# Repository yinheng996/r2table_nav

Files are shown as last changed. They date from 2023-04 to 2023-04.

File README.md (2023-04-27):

# Robotic Food Delivery System

This is an open-source project for a Robotic Food Delivery System, developed as part of the __EG2310 Fundamentals of System Design__ module, Sem 2 AY22/23, under the _Innovation and Design Programme (iDP)_ at National University of Singapore (NUS).

The project team, Studio 2 Group 3, comprises of Loh Yin Heng, Wang Bo, Jeanette Sim Yu, Hang Jin Guang, and Ananya Agarwal.

## Description
Our objective is to build a food delivery robot that seamlessly navigates through a restaurant, collects an order, and delivers it to the designated table. Our design is based on the Turtlebot 3 platform and utilizes ROS 2 Foxy as its operating system. We employ the MQTT messaging protocol for inter-system communication.

To achieve our objective, we have built a dispenser equipped with a keypad that allows for the selection of the table. Our dispenser is powered by an ESP32 microcontroller, which serves as the brain of the dispenser. This allows for seamless communication between the dispenser and the robot, and enables us to easily modify and update the dispenser's functionality.
<br>
<br/> <p align="center">
     
<br/>

<br>This repository houses the code for robot navigation, MQTT communication and dispenser functions.
You may check out our project report under the [/Documentations](https://github.com/yinheng996/r2table_nav/tree/main/Documentations) folder for more details on our robot and its mission.

## Important Files
* [disp_code.ino](https://github.com/yinheng996/r2table_nav/blob/main/ESP32_disp/disp_code.ino) - This file serves as the dispenser master script, responsible for powering the entire dispenser. It encompasses a range of functions including integration of the keypad, servo, and limit switch, in addition to the publisher code for MQTT. <br/>
* [limit_switch.py](https://github.com/yinheng996/r2table_nav/blob/main/py_pubsub_robot/limit_switch.py) - This file contains the code to be run on the RPi. It is in charge of publishing the limit switch status out to the remote laptop to let the remote laptop know when food has been removed from the carrier and to return to the dispenser so that it can take the next order.<br/>
* [r2tcheckpt_nav.py](https://github.com/yinheng996/r2table_nav/blob/main/table_nav/table_nav/r2tcheckpt_nav.py) - This file the master navigation script that we run on the laptop. It subscribes to MQTT and ROS topics and navigates the TurtleBot based on Table Number inputted on the dispenser. The main functions used to navigate around the restaurant setting is `move_til()` and `right_angle_rotate()`.  The important functions used to complete the task includes `connect_mqtt()`, `docking()`, `check_dist()`, `calibrate()` and `locate_table6()` <br/>
* [ESP32_test](https://github.com/yinheng996/r2table_nav/tree/main/ESP32_test) - This folder contains a series of C++ files that facilitate testing of the hardware functionality on the dispenser. Included are files to test the ESP32 blink, keypad, limit switch, MQTT publisher, servo and wifi setup.
* [r2factory_test.py](https://github.com/yinheng996/r2table_nav/blob/main/table_nav/table_nav/r2factory_test.py) -  This file contains a set of tests designed to verify the functionality of the TurtleBot. Upon execution, step-by-step instructions are displayed on the terminal for users to follow along.

## Preparation
### Installation
1. Follow the instructions here to setup ROS 2 Foxy on laptop and TurtleBot. <br/>
    (You may stop once you are able to teleoperate the TurtleBot from your computer.) <br/> 
    https://emanual.robotis.com/docs/en/platform/turtlebot3/quick-start/
2. Follow the instructions here to download, install and setup MQTT X on your laptop. <br/>
    (We are using a cloud-based MQTT desktop client for this project (MQTT X) for better consistency.) <br/> 
    https://github.com/emqx/MQTTX/blob/main/docs/manual.md <br/>
   Refer to our project configurations [here](https://github.com/yinheng996/r2table_nav/blob/main/Documentations/MQTT%20X%20Setup%20Config.pdf)
3. Follow the instructions here to setup ESP32 software. <br/> 
    https://esp32io.com/tutorials/esp32-software-installization
5. Follow the instructions here to setup Arduino IDE on your laptop. <br/> 
    https://www.arduino.cc/en/software <br/>
    Install the follow libraries on your Arduino IDE:
    * PubSubClient by Nick O'Leary
    * EspMQTTClient by Patrick
    * Keypad by Mark
    * ESP32Servo by Kevin
    * ezButton by ArduinoGetStarted.com
5. Follow the instructions here to setup Paho-MQTT on your laptop. <br/>
https://pypi.org/project/paho-mqtt/
6. Refer to our [/Hardware/Electrical Circuits](https://github.com/yinheng996/r2table_nav/tree/main/Hardware/Electrical%20Circuits) folder for the schematics of the circuits that we use to replicate our robot and dispenser system. <br/>
7. Refer to our [/Hardware/Mechanical Parts](https://github.com/yinheng996/r2table_nav/tree/main/Hardware/Mechanical%20Parts) folder for the fabrications and assembly that we use to replicate our robot and dispenser system. <br/>

__Important__: Please note that our project has been developed using Ubuntu 20.04.4, ROS2 Foxy, Arduino 2.1.0 and Python 3.6, as well as a DOIT ESP32 Devkit V1 Board and a Robotis Co. TurtleBot3 Burger with Raspberry Pi 3B+. As such, modifications may be necessary when using other software systems or hardware platforms.

### Setup

1. To setup your Ubuntu Machine, clone our repository into your Home directory. Compile the workspace. <br/>

    ```
    cd colcon_ws/src/auto_nav
    git clone https://github.com/yinheng996/r2table_nav.git 
    cd colcon_ws
    colcon build
2. To setup your TurtleBot, copy the `/py_pubsub` folder onto the Raspberry Pi. Compile the workspace. <br/>
    
    ```
    ssh ubuntu@<RPi IP address>
    scp -r <path to r2table_nav directory>/py_pubsub ubuntu@<RPi IP address>:~/turtlebot_ws/src 
    cd turtlebot3_ws
    colcon build 
3. To setup the ESP32, we will use the Arduino IDE.
    1. Open the code for the ESP32 in the Arduino IDE. This will be located in the repository that you cloned in step 1. In the code, make any necessary changes or modifications.
    2. Connect the ESP32 to your computer using a USB cable.
    3. In the Arduino IDE, select the correct board and serial port. To do this, navigate to `Tools` -> `Board` and select `ESP32 Dev Module`. Then, navigate to `Tools` -> `Port` and select the correct serial port.
    4. To upload the code onto the ESP32, click on the `Upload` button in the Arduino IDE and hold down BOOT button on esp32, release the button once u see "connecting" in the serial monitor.
    5. Once the upload is complete, disconnect the ESP32 from your computer and power it using an external power source. The code should now be running on the ESP32.
4. To setup MQTT X, launch the MQTT X Desktop Client
    1. After the connection to ESP32 is successful, click the `New Subscription` button in the lower left corner to add New Topics. <br/>
    2. Add the topics `docking` and `table_num`
## System check

#### For your TurtleBot
We need to test if the limit switch is connected to the RPi and if the RPi is able to publish its status using [limit_switch.py](https://github.com/yinheng996/r2table_nav/blob/main/py_pubsub_robot/limit_switch.py)
##### In one terminal
    ssh ubuntu@<RPi IP address>
    roslaunch turtlebot3_bringup turtlebot3_robot.launch
##### In another terminal
    ssh ubuntu@<RPi IP address>
    cd <path to r2table_nav directory>/py_pubsub
    python3 limit_switch.py
The terminal should start publishing the limit switch state, press and release the limit switch and check if the publisher updates the limit switch state.
If not, reboot your TurtleBot and repeat the TurtleBot system Check.
#### For your Laptop
We need to run a factory test on the TurtleBot from the Laptop to test if the laptop is able to communicate with the RPi and if all components of the TurtleBot is functional using [r2factory_test.py](https://github.com/yinheng996/r2table_nav/blob/main/table_nav/table_nav/r2factory_test.py).
##### In one terminal
    cd <path to r2table_nav directory>/table_nav/table_nav
    python3 r2factory_test.py
Follow the instructions printed on your terminal, and if everything works out fine, it means the system is ready to go.
#### For your ESP32
We need to run a factory test on the ESP32. <br/>
   Launch the ESP32 factory test scripts in our [/ESP32_test](https://github.com/yinheng996/r2table_nav/tree/main/ESP32_test) folder onto your Arduino IDE, then upload and run on your ESP32 module. <br/>
   Do this individually for each script. <br/>
   If your ESP32 module passes all the tests, it is ready to go.
#### For your MQTT X
We need to check if the MQTT is able to received messages from the ESP32. <br/>
   Launch the MQTT desktop client. <br/>
   Check for messages received from the ESP32 Publisher. If nothing is received, refresh the desktop client. <br/>

## Operation Parameters
From lines 15 to 41 of [/table_nav/table_nav/r2tcheckpt_nav.py](https://github.com/yinheng996/r2table_nav/blob/main/table_nav/table_nav/r2tcheckpt_nav.py)

The explanation of all the parameters are as commented below. These are the values which we found work the best for us in our use case. Please change these values if you require a different behavior of the robot.

    # Constants
    FAST_ROTATION_SPEED = 0.5 # speed of fast rotation, mainly for regular turns
    SLOW_ROTATION_SPEED = 0.2 # speed of slow rotation, mainly for calibrations
    MOVING_SPEED = 0.18 # speed of linear movements

    LIDAR_FRONT_OFFSET = 0.193 # distance from lidar to front of robot
    LIDAR_BACK_OFFSET = 0.094 # distance from lidar to back of robot
    DISPENSER_WALL_DISTANCE = 0.50 # distance from centre of dispenser to wall
    STOP_DISTANCE = 0.1 + LIDAR_FRONT_OFFSET # distance to stop from Table

    CORF_OFFSET = 0.152 # distance from centre of rotation to front of robot
    CORB_OFFSET = 0.13 # distance from centre of rotation to back of robot

    DOCKING_DIST = 0.178 # distance to stop from docking station

    MOVE_DIST_F = LIDAR_FRONT_OFFSET + 0.21 # movement offset at speed 0.18 from front
    MOVE_DIST_CORF = MOVE_DIST_F - CORF_OFFSET # movement offset at speed 0.18 from centre of rotation from front
    MOVE_DIST_B = LIDAR_BACK_OFFSET + 0.24 # movement offset at speed -0.18 from back
    MOVE_DIST_CORB = MOVE_DIST_B - CORB_OFFSET # movement offset at speed -0.18 from centre of rotation from back

    SWEEP_ANGLE = 30 # angle to sweep for Table
    ANGLE_RANGE = range(-SWEEP_ANGLE, SWEEP_ANGLE + 1) # range of angles to sweep for Table

    LIDAR_DATA_FILE = 'lidar.txt' # file to store lidar data logged
    MAP_DATA_FILE = 'map.txt' # file to store map data logged

    CAN_DROP = 4 # seconds to wait before can is dropped

From lines 43 to 49 of [/table_nav/table_nav/r2tcheckpt_nav.py](https://github.com/yinheng996/r2table_nav/blob/main/table_nav/table_nav/r2tcheckpt_nav.py)

Please input your MQTT configurations, especially your username and password.

    # MQTT variables
    MQTT_BROKER = "broker.emqx.io"
    MQTT_PORT = 1883
    MQTT_USERNAME = "idpgrp3" # username for MQTT broker
    MQTT_PASSWORD = "turtlebot" # password for MQTT broker
    MQTT_TOPIC_TABLENUM = "table_num" # topic to subscribe to for table number
    MQTT_TOPIC_DOCKING = "docking" # topic to subscribe to for docking

## Running the Code
A total of __4 terminals__ would be required to run the code, in addition to the __MQTT X desktop client__. <br/> 
Prior to commencing the operation, ensure that a stable WiFi connection is established and that all devices, including the ESP32, laptop, and TurtleBot, are connected to the same WiFi network. It is critical to verify that all electrical connections are secure, and all mechanical mountings on both the TurtleBot and Dispenser are firmly in place before initiating the operation. <br/>
__To ensure reliable and safe performance, it is advised to avoid any physical contact with the system during operation.__ <br>
##### In Terminal 1: To bring up TurtleBot3
    ssh ubuntu@<RPi IP address>
    roslaunch turtlebot3_bringup turtlebot3_robot.launch
##### In Terminal 2: To host Bot Limit Switch Publisher
    ssh ubuntu@<RPi IP address>
    cd <path to r2table_nav directory>/py_pubsub_robot
    python3 limit_switch.py
##### In Terminal 3: To host IR Sensor Publisher
    ssh ubuntu@<RPi IP address>
    cd <path to r2table_nav directory>/py_pubsub_robot
    python3 IR.py
##### In Terminal 4: To run navigation code
    cd <path to r2table_nav directory>/table_nav/table_nav
    python3 r2tcheckpt_nav.py
#### In MQTT X:
* Launch MQTT X and select `connect`. <br/>
<br>
The system is ready to go. Press a number from 1-6 on the keypad for Food Delivery.

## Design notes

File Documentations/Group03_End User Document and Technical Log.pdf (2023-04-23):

EG2310 GROUP 3 END USER DOCUMENT AND TECHNICAL LOG

### 1. General System Description and Critical Data

Purpose: The Dispenser and Delivery Robot System allows a can to be loaded, dispensed, and then delivered to a table chosen by the user.

### 1.1 Dispenser

The Dispenser allows the user to load a can, choose the table number for delivery. It then transfers the can to the Delivery Robot.
Model | Custom-made in-house
Overall Weight | 1.64 kg
Overall Centre of Gravity w/o can (x,y,z) | (35.59, 82.25, 30.16)
Overall Dimension LxWxH (mm) | 93x178x207
Power Specification | 4x AAA Batteries

### 1.2 Delivery Robot

The Delivery Robot is designed to receive a ⌀66mm drink can of length 115mm, approx weight 350g from the Dispenser and delivers it to the table chosen by the user. The manufacturer does not guarantee the usability of this robot for cans of different dimensions and/or weights.
Model | ROBOTIS TurtleBot 3 Burger adapted with custom-made Drink Can Carrier Assembly
Software Version | Ros2 Foxy
Overall Weight | 1.3kg
Overall Centre of Gravity w/o can (x,y,z) | (5.5,0,5.5)
Overall Dimension LxWxH (mm) | 235x178x192
Power Specification | LiPo Battery 11.1V 1,800mAh

Refer to TurtleBot3 Burger Specifications found on ROBOTIS e-Manual website: https://emanual.robotis.com/docs/en/platform/turtlebot3/features/#specifications

### 1.3 Instructions for User

1) Place Dispenser at the designated spot on the arena such that its center is 50cm from the side wall and the Electronics Platform is flush to the back wall of the designated spot.
2) Place the Delivery Robot in front of the Dispenser such that the front of the LiDAR is facing the Dispenser and the V-shaping Homing Plate on Delivery Robot is inside the Dispenser’s V-shaping Homing Plate. Do not press any buttons before this is done.
3) Load the can in the Dispenser. Do not drop in the can, place it lightly in the carrier, flushed close to the servo-side.
4) Press the button labeled ‘EN’ on the ESP32 board.
5) Press the button on the keypad to indicate the table number. Do not press the button multiple times. You can only press table number 1-6 and each table can only be chosen once. If a table that has been chosen before must be chosen again, follow steps in 1.4
6) Dispenser will load the can into the robot, and the robot will travel to the designated table. It may go near other tables, please wait until it reaches the desired table and the wheels have stopped rotating to pick up the can.
7) Collect the can after the robot comes to a full stop within 15cm of the designated table.
8) Wait for the Delivery robot to return to the dispenser and dock with the dispenser.
9) Repeat Steps 5-9 for subsequent tables.

### 1.4 Repeating a table

1) On the back-end laptop, press ctrl+C. Press the arrow up key and press enter.

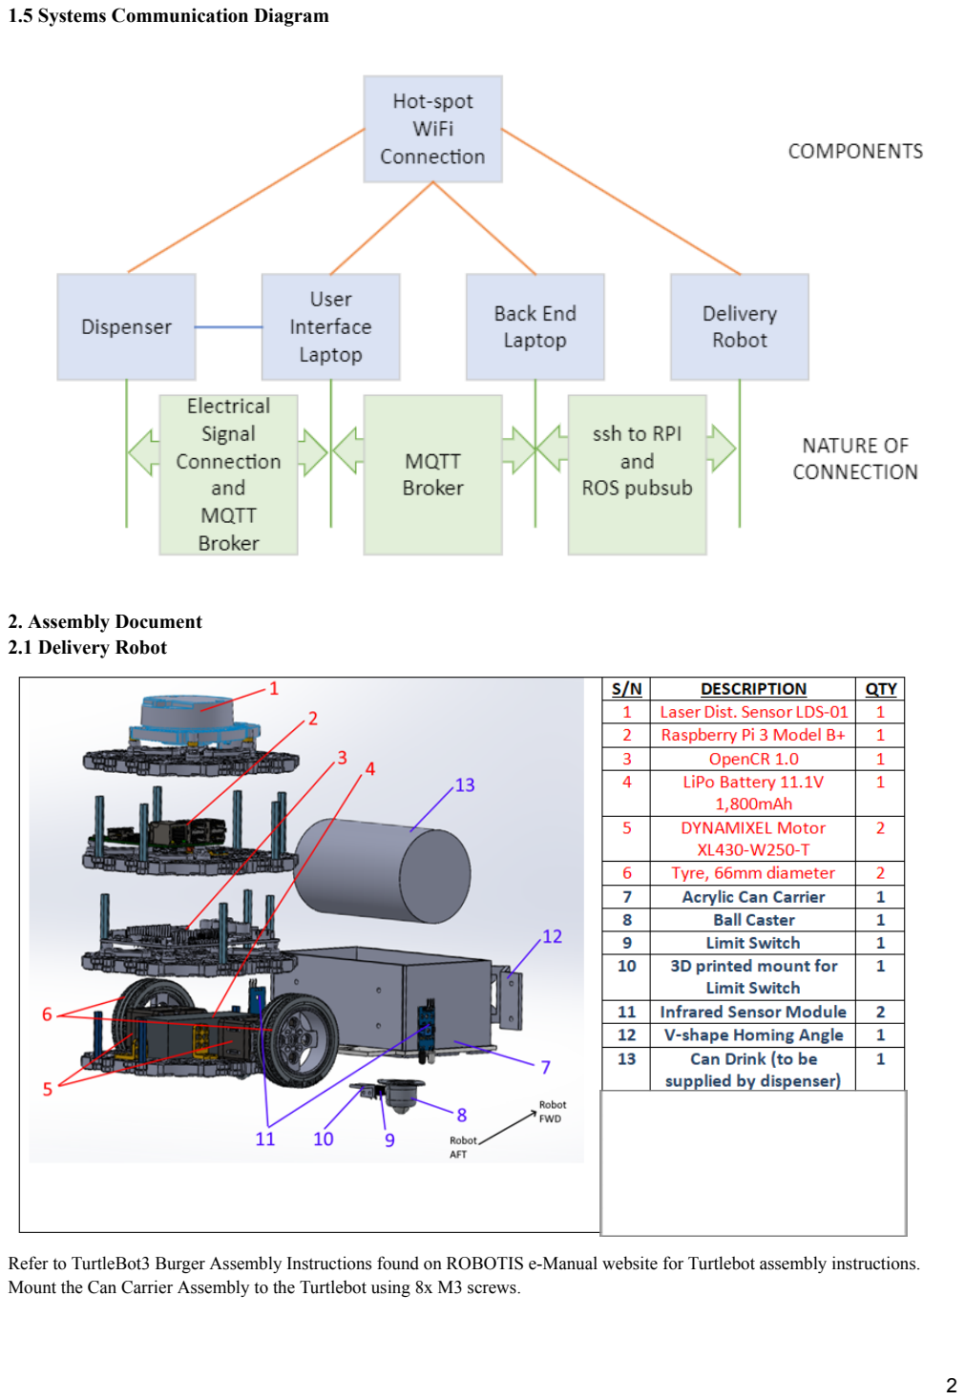
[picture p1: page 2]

### 1.5 Systems Communication Diagram

### 2. Assembly Document 2.1 Delivery Robot

Refer to TurtleBot3 Burger Assembly Instructions found on ROBOTIS e-Manual website for Turtlebot assembly instructions. Mount the Can Carrier Assembly to the Turtlebot using 8x M3 screws.

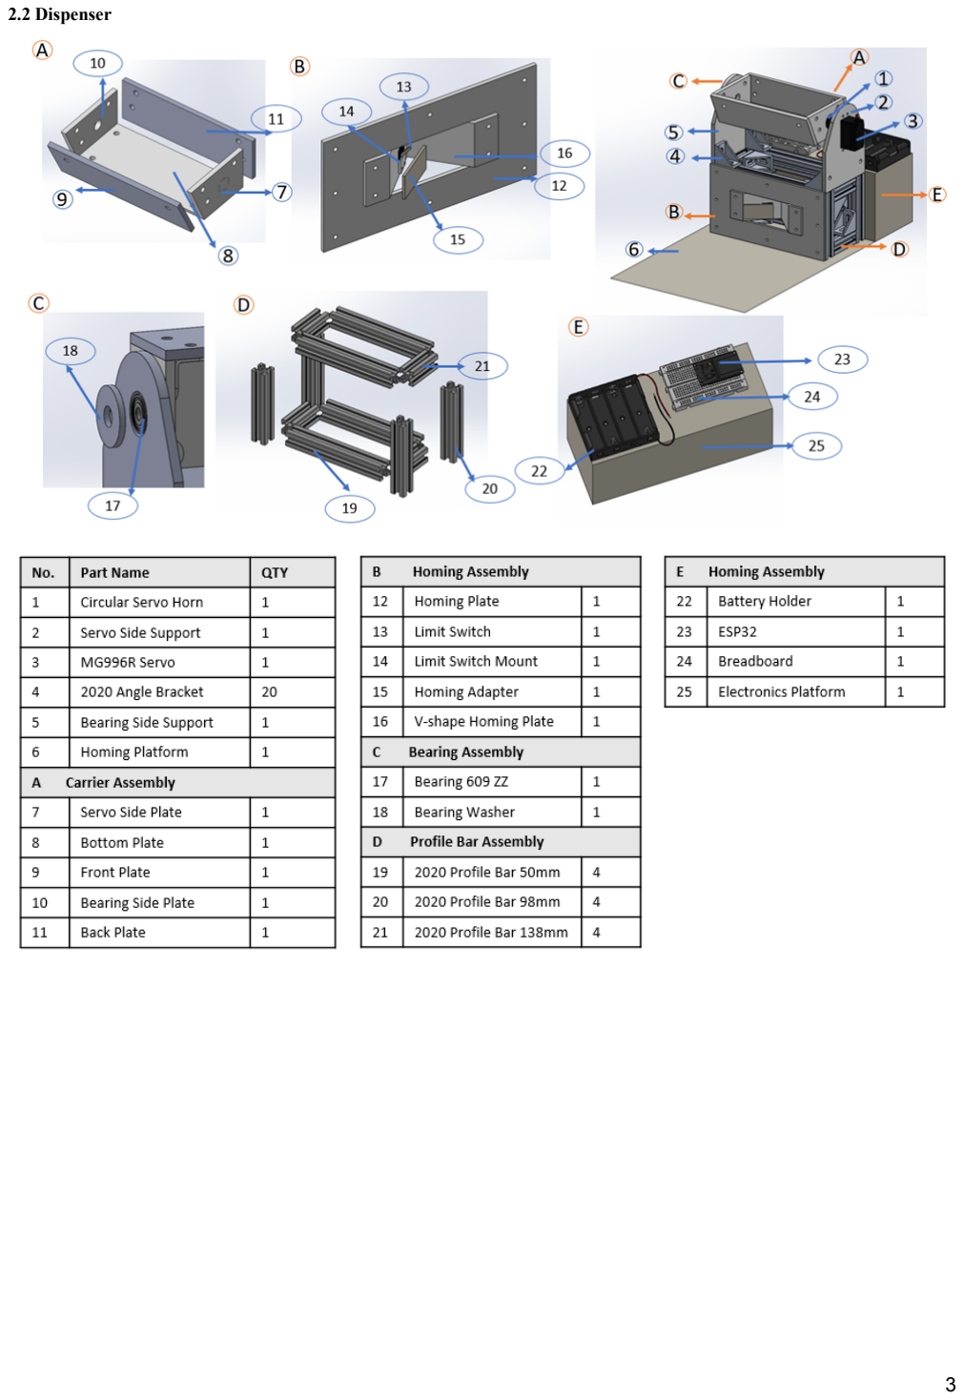
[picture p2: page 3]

### 2.2 Dispenser

### 3. Acceptable Defect Log

### 3.1 Dispenser

Defect Description | Acceptable Criteria | Defect Classification
Critical | Major | Minor
Dispenser carrier has gaps between its faces | This does not pose any effects on its structural integrity, strength of holding the can, and general function | | X
Homing Angle has a cardboard piece taped inside | This serves to facilitate the homing | | | X
Profile bar base has slight misalignment | This does not affect its structural integrity | | | X
The nut for the bearing is a little lose | This is to ensure tolerancing for proper function of the roller bearing | | X

### 3.2 Delivery Robot

Defect Description | Acceptable Criteria | Defect Classification
Critical | Major | Minor
There is acrylic glue holding the plates of the Delivery Robot’s carrier together but there are slight gaps | Tape is used to ensure the carrier is secure | | | X
LiDAR scanning is not accurate | We have calibration code to check that the LiDAR is operating correctly in relation to its surroundings. | | X

### 4. Factor Acceptance Test

### 4.1 Dispenser

Test Procedure and Objectives | Acceptable Criteria | Acceptable (Y/N)

Physical Checks

Shake test | When the Dispenser is shook, no cables come loose, no parts fall out, no screws fall out
Safety Check | No signs of damage on the cables Cables are routed neatly and are not in the way of the Dispenser Carrier’s motion
Common Ground | Ensure all components are connected to common ground

Electronics Components Checks

Connect a laptop with the Arduino IDE, running ‘ESP32_final_mqtt_pub_test’ to the ESP32

Verify Batteries are in working condition | Use multimeter to ensure batteries that the sum of the 4 AA Batteries sum to at least 4.8 V
Verify that the limit switch works | Press down the limit switch. Serial Monitor on laptop screen should print ‘Limit switch activated! Robot is here, waiting for

| keypad input…’
Verify that the keypad works | Press any key from 1 to 6. Serial Monitor on laptop screen should print ‘Table number for delivery: [keypad input]’
Verify that the Servo motor works | After the laptop screen prints ‘Robot is receiving table number...’, it should print ‘Tilting…’ and the servo should turn the Dispenser Carrier

### 4.2 Delivery Robot

Test Procedure and Objectives | Acceptable Criteria | Acceptable (Y/N)

Physical Hardware Checks

Shake test | When the Delivery Robot is shook, no cables come loose, no parts fall out, no screws fall out
Safety Check | No signs of damage on the cables
Turn on Delivery Robot | 1. Green light on the OpenCR 2. Sequence of beeps in when Turtlebot is turned on 3. RPI Green Light is on

Electronics Components Checks

Verify that the RPi works | Sshrp to the RPI Terminal should return ‘Welcome to Ubutntu [...]’ RPI flashes a red light to show power is connected RPI flashes a green light to show SD card is being read
Verify that the OpenCR works | Sequence of beeps when the delivery robot is turned on
Verify that the Dynamixel motors work | Key in ros2 run turtlebot3_teleop teleop_keyboard The following commands can be used to observe that the movement is as expected W for forward S for Stop D for turning right A for turning left X for backwards
Verify that the IR Sensor Module is operational | The IR sensor on one side should be light up green and the other side should light up red.
Verify that the LiDAR is calibrated correctly | Key in python3 r2lidar_calib.py Key in ‘0’ and place an object at the physical ‘0’ degree of the LiDAR. The LiDAR should be logging a sudden decrease in distance (0.21), which indicates that the angle is calibrated. Repeat for 180 degrees, you should see the distance as 180 degrees

### 5. Maintenance and Part Replacement Log

FOUND BY/DATE /TIME/SIGN | REASON PLACED UNSERVICEABLE | DETAILS OF ACTION TAKEN | DATE/ TIME | TRADESMAN NAME/SIGN
HANG JG 30/3/23 2030H | BATTERY UNABLE TO CHARGE. | BATTERY REPLACED. | 30/3/23 2045H | HANG JG

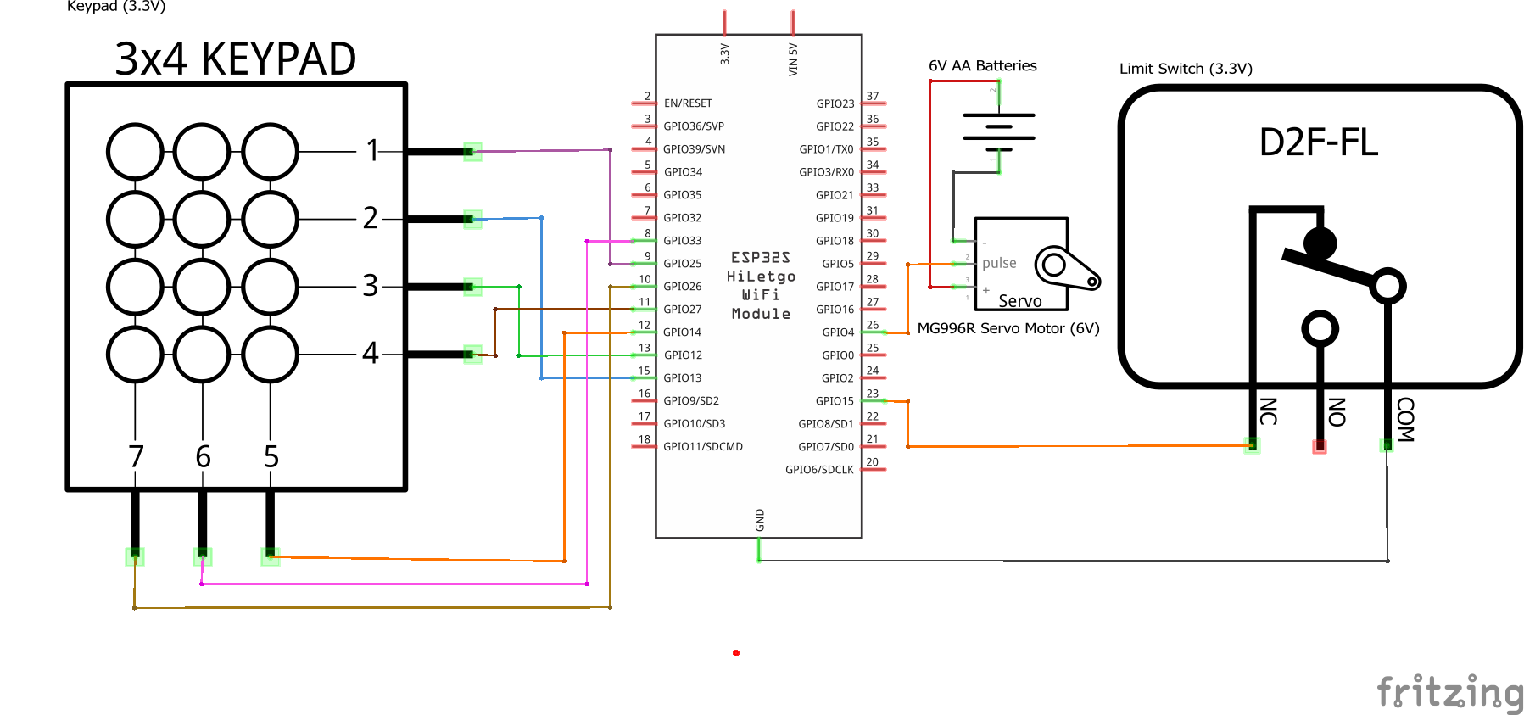
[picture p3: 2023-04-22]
Hardware/Electrical Circuits/ESP32_WROOM_32 Dispenser System - Schematics.png

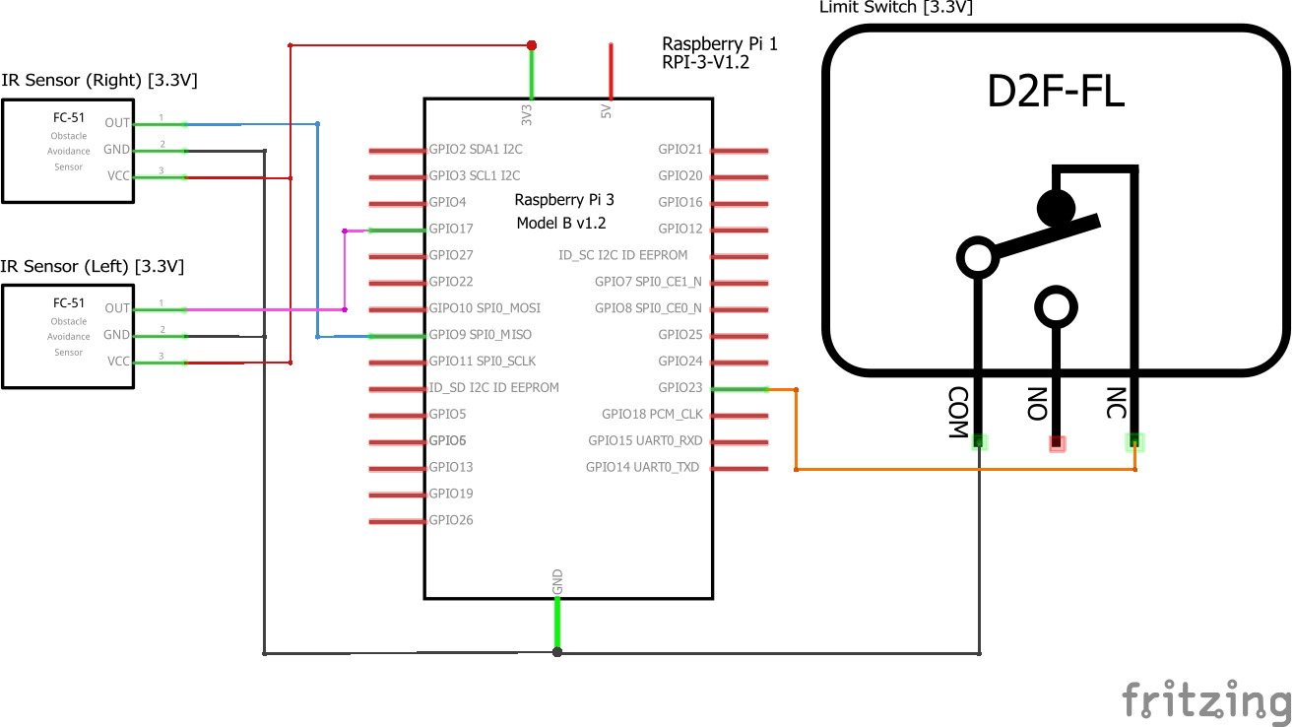
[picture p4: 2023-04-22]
Hardware/Electrical Circuits/Delivery Robot System - Schematics.png

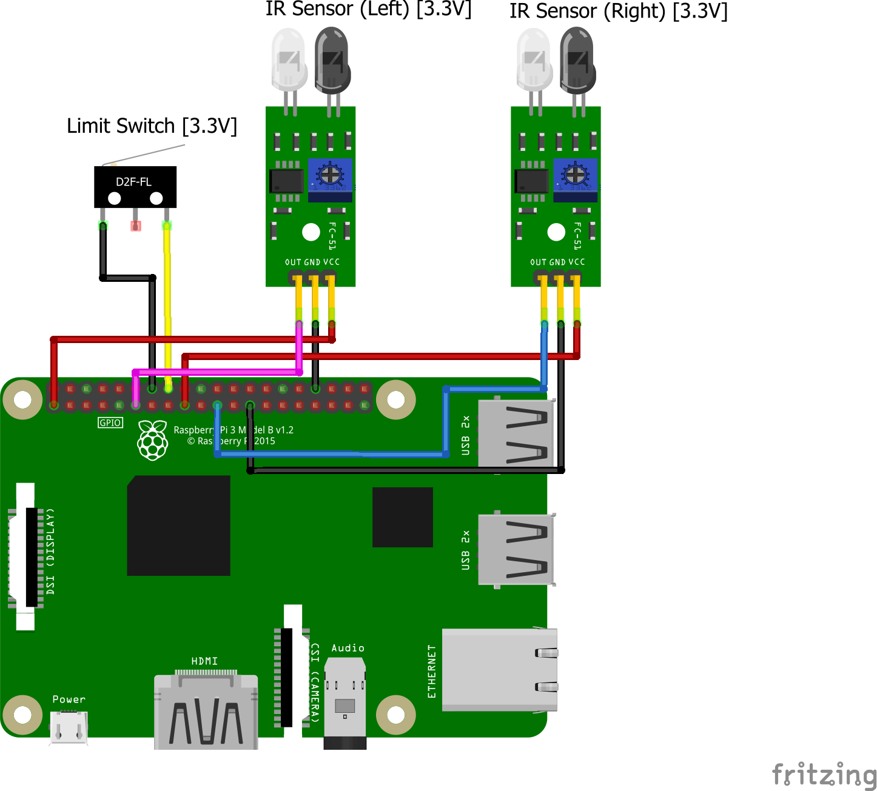
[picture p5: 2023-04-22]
Hardware/Electrical Circuits/Delivery Robot System - Breadboard.png

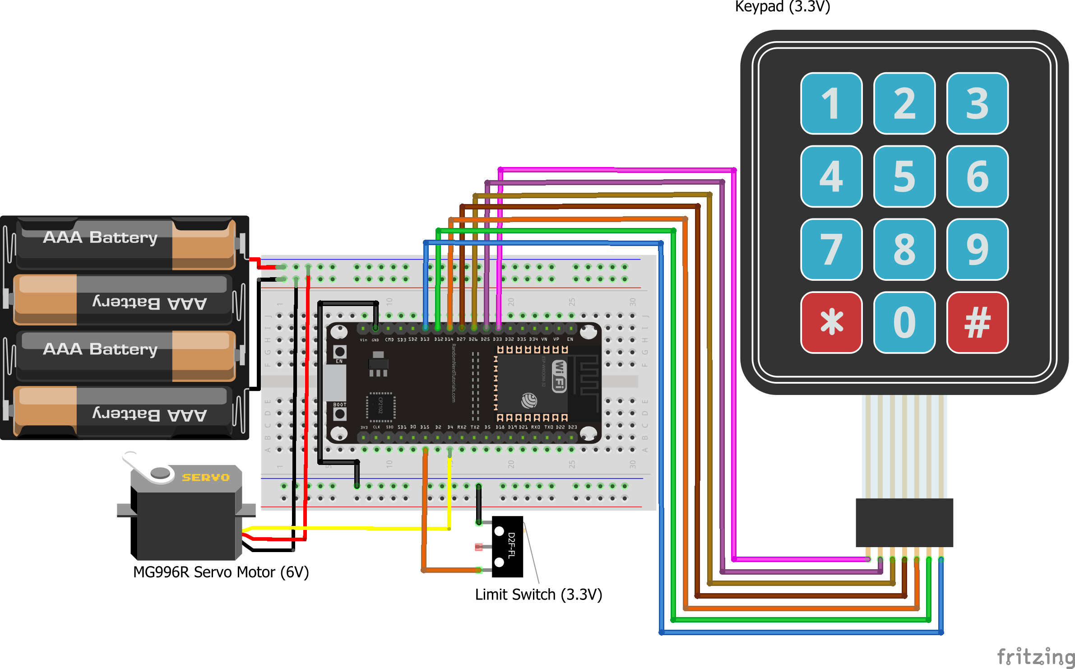
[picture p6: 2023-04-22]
Hardware/Electrical Circuits/ESP32_WROOM_32 Dispenser System - Breadboard.png

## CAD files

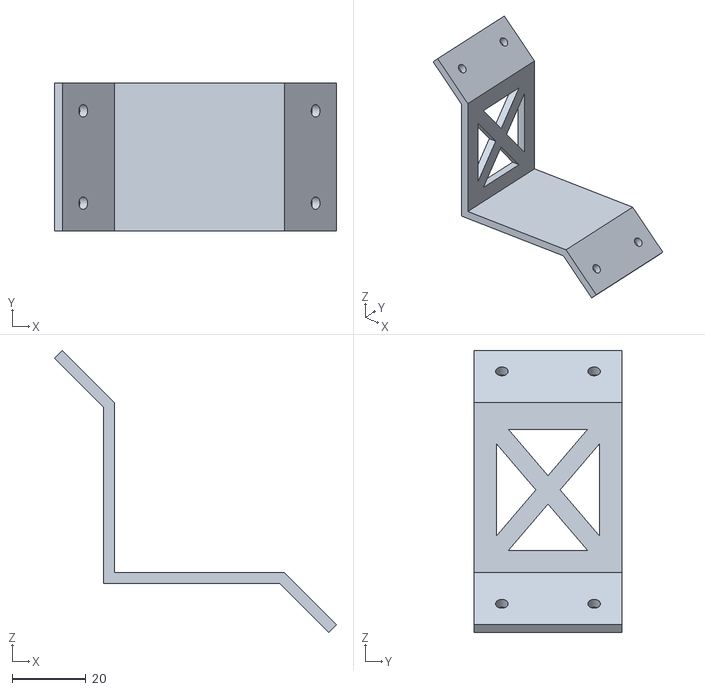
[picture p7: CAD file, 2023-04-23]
Hardware/Mechanical Parts/3D_Print/Homing L Robot-side Split.STL
76.4 x 40.0 x 76.4

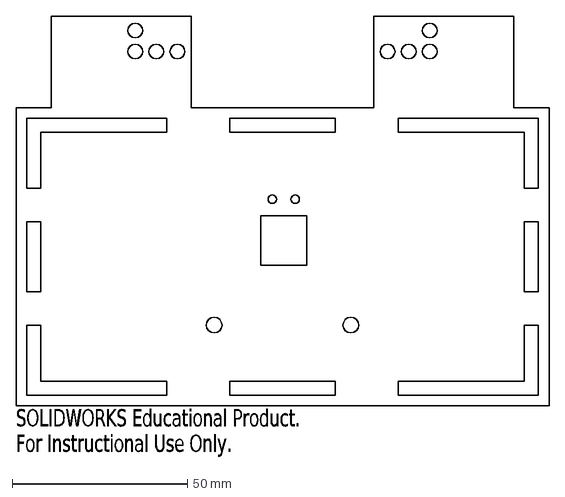
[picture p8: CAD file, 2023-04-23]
Hardware/Mechanical Parts/Robot_Can_Carrier/[Trayv2] Base_T5_Qty1.DXF
SOLIDWORKS Educational Product.
For Instructional Use Only.

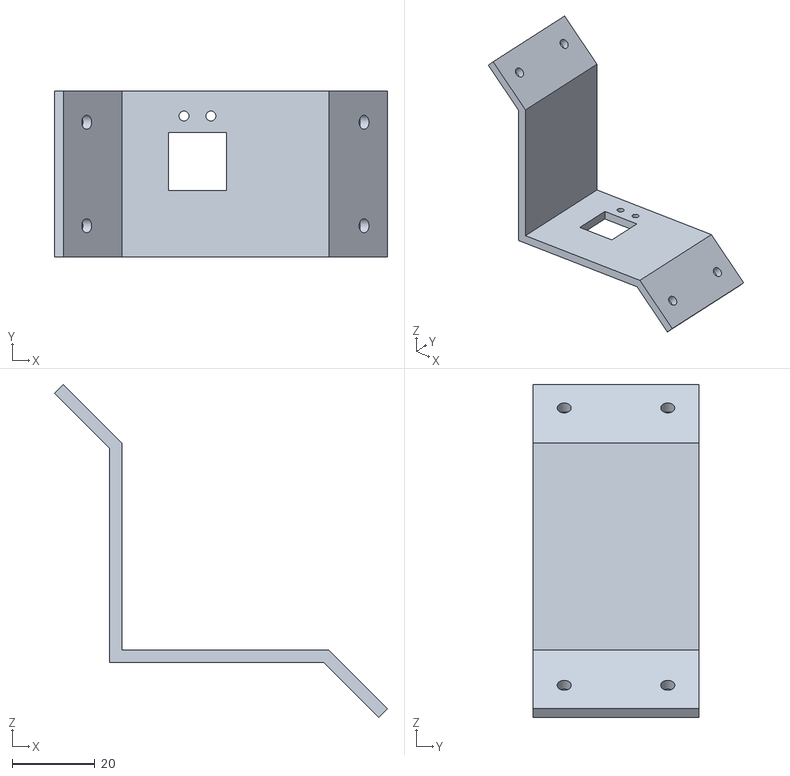
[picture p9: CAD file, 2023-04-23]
Hardware/Mechanical Parts/3D_Print/Homing L.STL
80.4 x 40.0 x 80.4

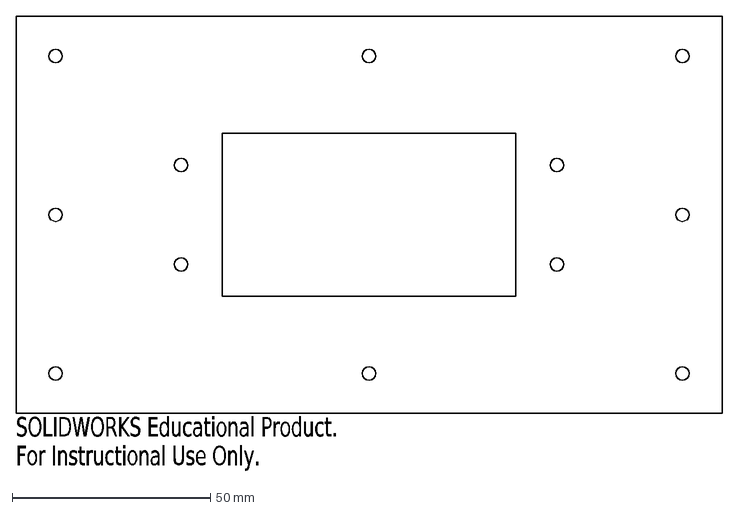
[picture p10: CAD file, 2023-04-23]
Hardware/Mechanical Parts/Dispenser/Robot Homing Plate_T3mm_QTY1.DXF
SOLIDWORKS Educational Product.
For Instructional Use Only.

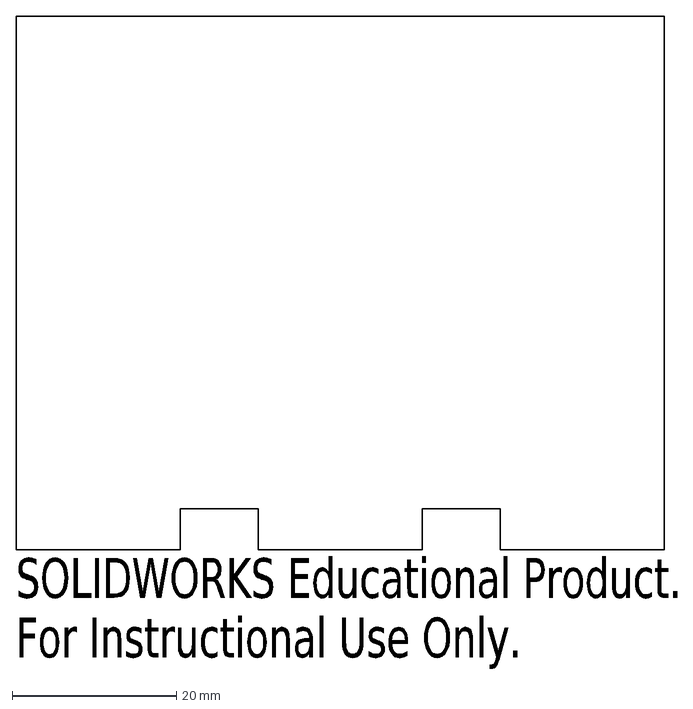
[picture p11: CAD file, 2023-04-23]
Hardware/Mechanical Parts/Robot_Can_Carrier/[Trayv2] short side_T3_Qty2.DXF
SOLIDWORKS Educational Product.
For Instructional Use Only.

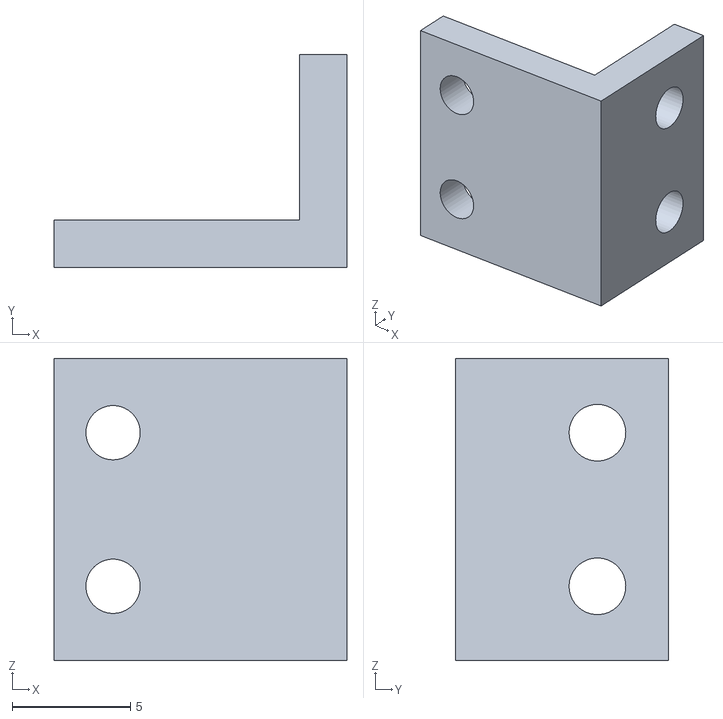
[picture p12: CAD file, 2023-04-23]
Hardware/Mechanical Parts/3D_Print/Limit Switch Mount Dispenser.STL
12.4 x 9.00 x 12.8

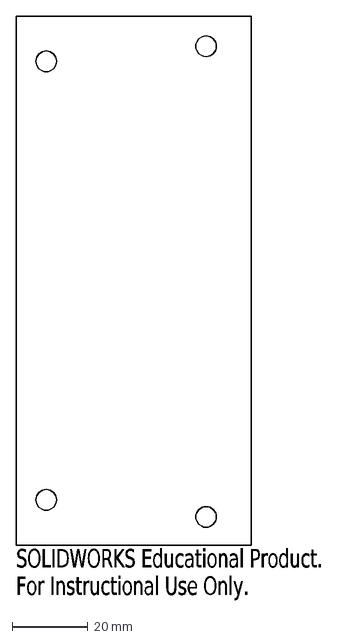
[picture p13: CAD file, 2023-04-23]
Hardware/Mechanical Parts/Dispenser/Bucket Base2_T5_QTY1.DXF
SOLIDWORKS Educational Product.
For Instructional Use Only.

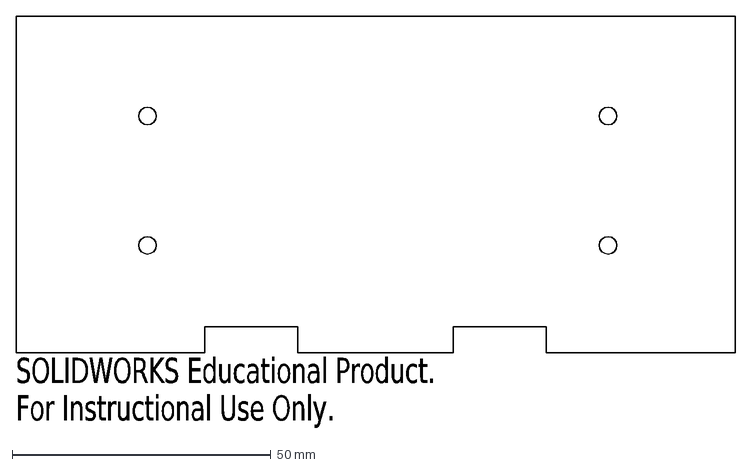
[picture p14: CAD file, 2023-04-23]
Hardware/Mechanical Parts/Robot_Can_Carrier/[Trayv2] Long side_T3_Qty2'.DXF
SOLIDWORKS Educational Product.
For Instructional Use Only.

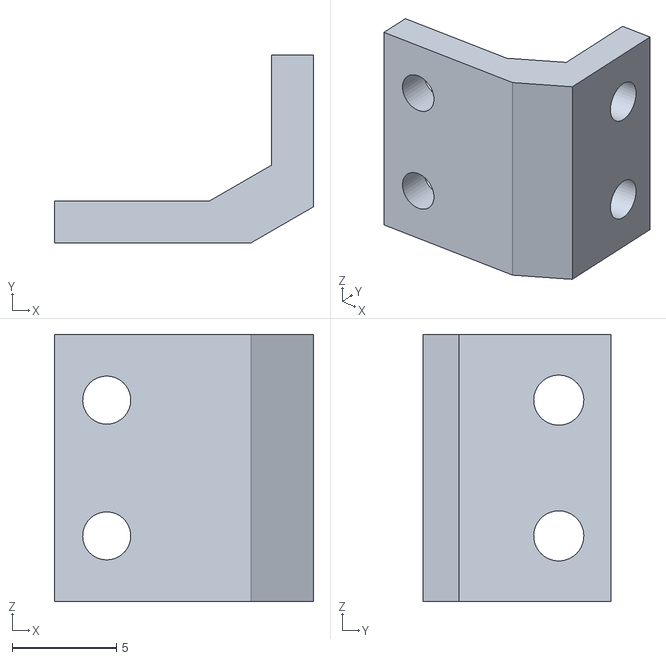
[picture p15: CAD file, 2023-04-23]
Hardware/Mechanical Parts/3D_Print/Limit Switch Mount Carrier.STL
12.4 x 9.00 x 12.8

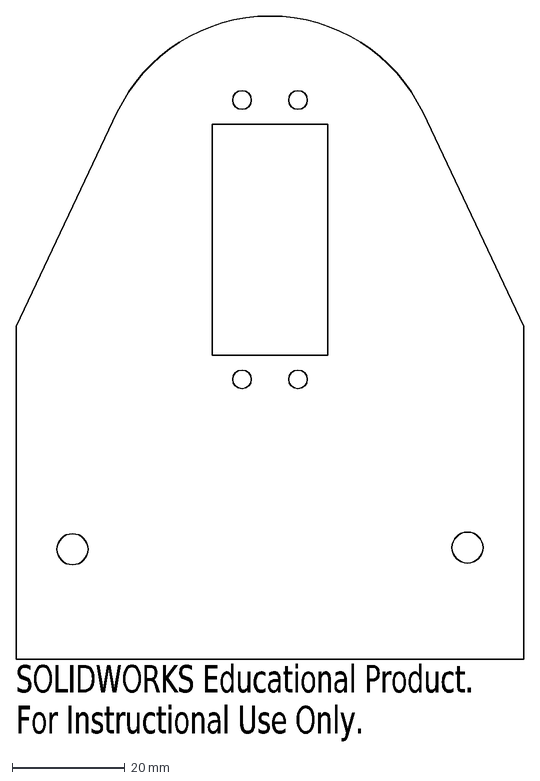
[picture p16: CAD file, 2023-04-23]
Hardware/Mechanical Parts/Dispenser/Side Support Servo Side Fri_T5_QTY1.DXF
SOLIDWORKS Educational Product.
For Instructional Use Only.

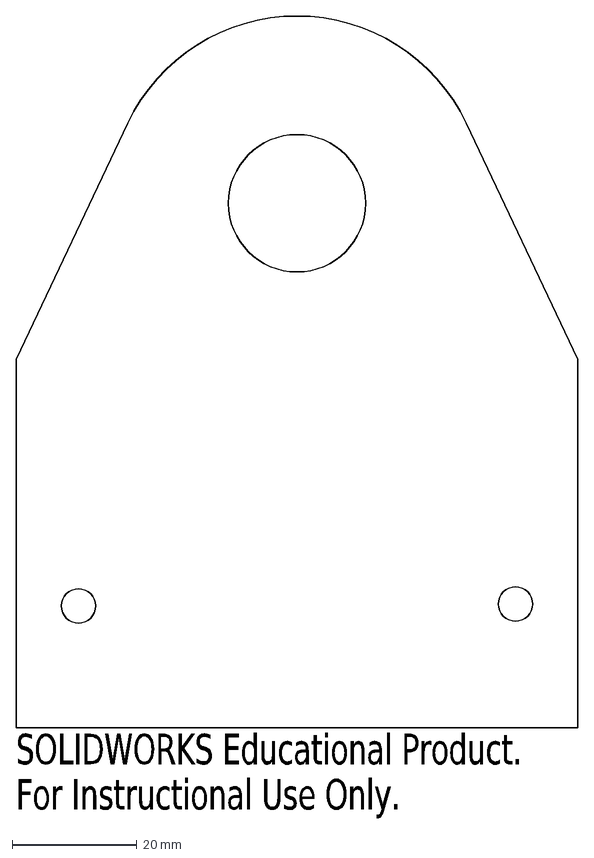
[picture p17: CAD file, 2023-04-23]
Hardware/Mechanical Parts/Dispenser/Side Support Bearing Side Fri_T5_QTY1.DXF
SOLIDWORKS Educational Product.
For Instructional Use Only.

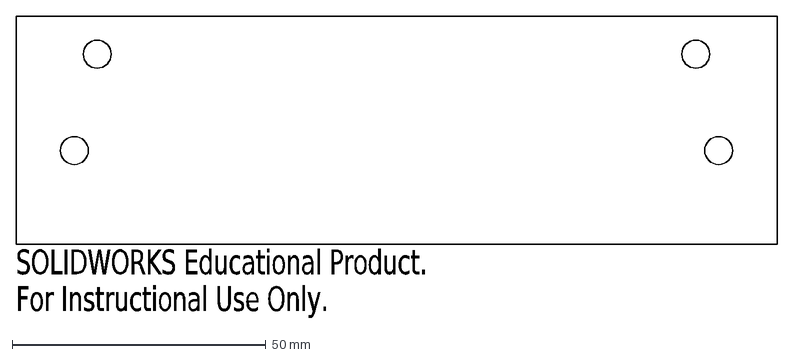
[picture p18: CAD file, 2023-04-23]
Hardware/Mechanical Parts/Dispenser/Back Carrier Acrylic_T5_QTY1.DXF
SOLIDWORKS Educational Product.
For Instructional Use Only.

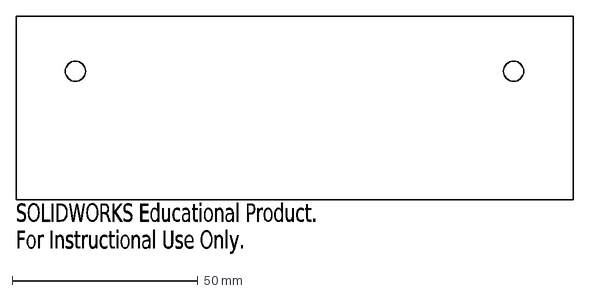
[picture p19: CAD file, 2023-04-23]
Hardware/Mechanical Parts/Dispenser/Front Carrier_T5_QTY1.DXF
SOLIDWORKS Educational Product.
For Instructional Use Only.

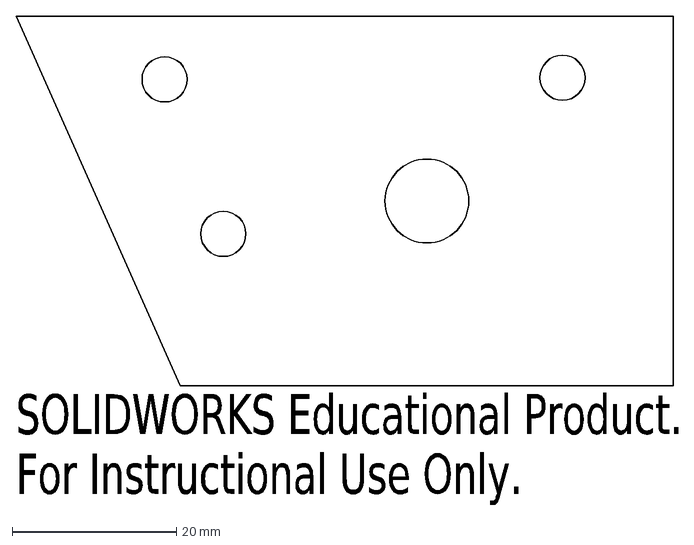
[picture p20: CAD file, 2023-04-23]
Hardware/Mechanical Parts/Dispenser/Bucket Bearing Side_T5_QTY1.DXF
SOLIDWORKS Educational Product.
For Instructional Use Only.

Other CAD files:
Hardware/Mechanical Parts/Dispenser/Bucket Servo Side_T5_QTY1.DXF
Hardware/Mechanical Parts/Dispenser/Bearing Washer_T3_QTY2.DXF

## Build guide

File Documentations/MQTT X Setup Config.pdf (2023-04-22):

## Client related information (basically filling in the settings according to the screenshot below)

After entering the creation page, it is required to configure or fill in the relevant information for connecting to the client.

1. Broker information (under General)

When configuring the Broker information,Client ID, Host, and Port are already filled in by default. You can also modify it by yourself based on the actual Broker information. Click the refresh button to the right of Client ID to quickly generate a new Client ID. The drop-down box in front of Host is used to select the connection protocol, which supports mqtt: //, ws: //. If an SSL / TLS authentication connection is used, it needs to be modified to mqtts: //. , Wss: //.
Note: When the protocol is modified, the connection port needs to be modified.
2. User authentication information (for username & password)

If your broker has enabled user authentication, you can fill in the information of Username and Password in the configuration item. (Username: idpgrp3; Password: turtlebot)

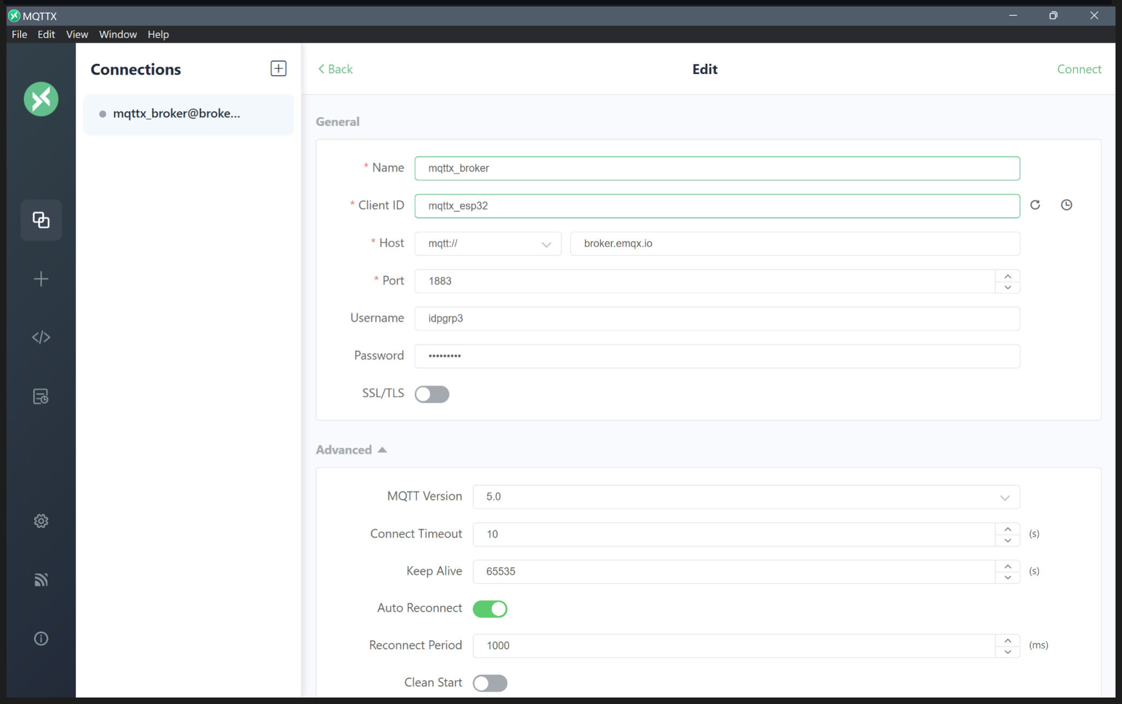
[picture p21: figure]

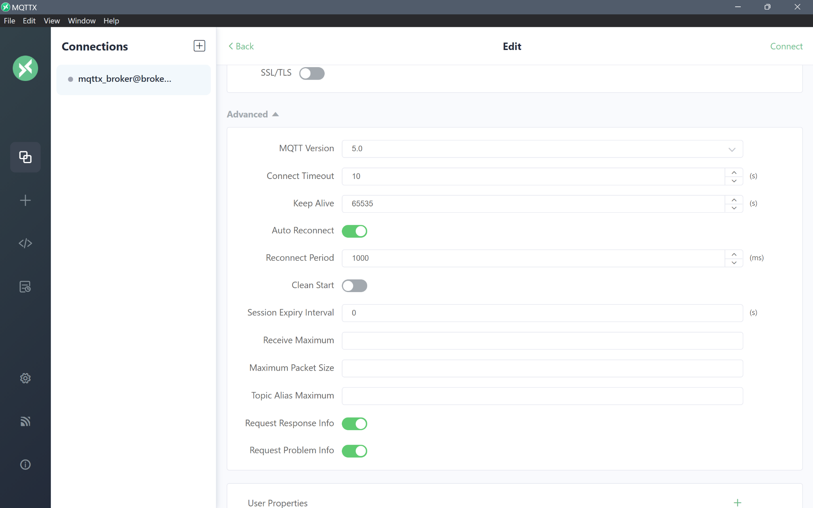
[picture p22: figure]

## Publish and subscription of message

1. Main interface

After the connection is successful, you can enter the main interface of the connection. Click the fold button next to the connection name at the top to expand and display some basic information of the configuration. It is convenient to quickly modify several commonly used configurations of the connection. You need to disconnect when modifying, and click connect again to take effect. After each successful connection, the panel will automatically fold up. In the disconnected state, you can also click the configuration button on the right to modify more connection configurations.

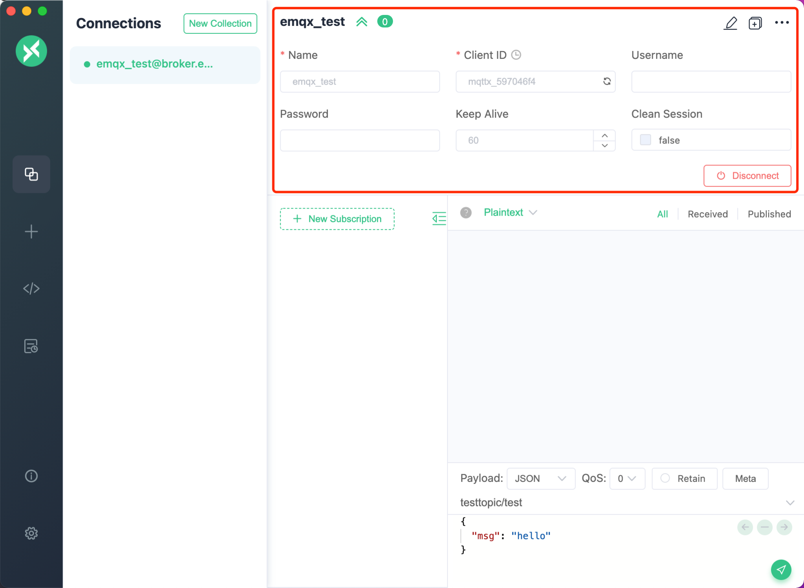
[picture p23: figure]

2. Add subscription

Click the New Subscription button in the lower left corner to quickly add a Topic. Each Topic can be marked with a color, which can be randomly generated or opened by the color selector. The rightmost button at the top of the subscription list can hide the subscription list to show more space on the page. After the addition is complete, click on the subscribed Topic items in the subscription list to achieve message filtering. The message view will only display the message content subscribed to the current topic. Click again to cancel the filter; You can also directly click other subscribed Topic items to view the corresponding message content. By clicking on the topic name, you can quickly copy the current topic information. When you need to send a message to this topic, you can quickly paste it into the topic input box of the message bar to modify it, and you can quickly complete the operation.

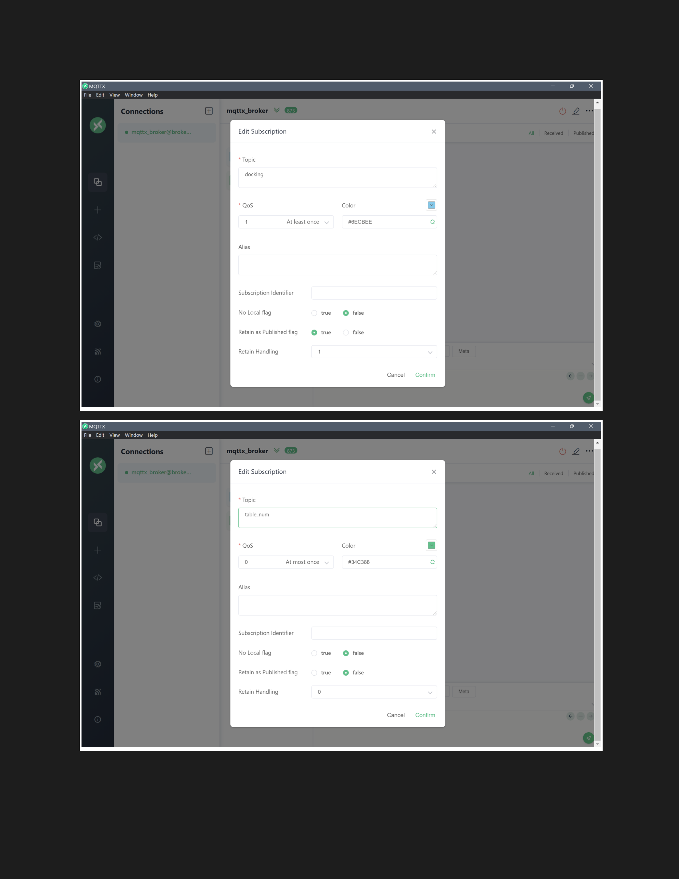
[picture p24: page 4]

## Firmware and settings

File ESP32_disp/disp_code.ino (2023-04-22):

#include <WiFi.h>
#include <PubSubClient.h>
#include <Keypad.h>
#include <ESP32Servo.h>
#include <ezButton.h>

//WiFi Network credentials
const char* ssid = "jntes";
const char* password = "mivi9960";

//MQTT Broker Settings
const char* mqtt_server = "broker.emqx.io";
const int mqtt_port = 1883;
const char* mqtt_username = "idpgrp3";
const char* mqtt_password = "turtlebot";
const char* mqtt_topic_tablenum = "table_num";
const char* mqtt_topic_docking = "docking";

//Keypad Setup
const byte ROWS = 4;
const byte COLS = 3;
char keys[ROWS][COLS] = {
  {'1','2','3'},
  {'4','5','6'},
  {'7','8','9'},
  {'*','0','#'}
};
byte rowPins[ROWS] = {33, 25, 26, 27};
byte colPins[COLS] = {14, 12, 13};
Keypad keypad = Keypad(makeKeymap(keys), rowPins, colPins, ROWS, COLS);

//Limit Switch Setup
ezButton limitSwitch(15);

//Servo Motor Setup
Servo servo;
int servoPin = 4;

//Initialize WiFi & MQTT client
WiFiClient espClient;
PubSubClient client(mqtt_server, mqtt_port, espClient);

unsigned long previousMillis = 0;
unsigned long interval = 30000;
unsigned long lastMsg = 0;
#define MSG_BUFFER_SIZE (5)
char msg[MSG_BUFFER_SIZE];

int tableNum = 0;
bool robot_arrived = false;
bool docking = false;

void setup_wifi() {
  delay(10);
  WiFi.begin(ssid, password);
  Serial.println();
  Serial.print("Connecting to WiFi..");
  while (WiFi.status() != WL_CONNECTED) {
    Serial.print(".");
    delay(1000);
  }
  randomSeed(micros());
  Serial.println("");
  Serial.println("WiFi connected");
  Serial.print("IP address: ");
  Serial.println(WiFi.localIP());
}

void reconnect() {
  //Loop until we're reconnected
  //client.connect returns a boolean value to let us know if the connection was successful.
  while (!client.connected()) {
    Serial.println("Attempting MQTT connection...");
    String clientId = "ESP32Client-";
    /*clientId += String(random(0xffff), HEX);*/
    if (client.connect(clientId.c_str(), mqtt_username, mqtt_password)) {
      Serial.println("Connected to MQTT Broker");
    } 
    else {
      Serial.print("Failed, rc=");
      Serial.print(client.state());
      Serial.println(" try again in 2 seconds");
      //Wait 5 seconds before retrying
      delay(2000);
    }
  }
}

void constantPublish() {
  //Publish Docking Status every 2 seconds
  unsigned long currentMillis = millis();
  if (currentMillis - lastMsg > 2000) {
    lastMsg = currentMillis;
    //Read Docking Status
    limitSwitch.loop();
    int state = limitSwitch.getState();
    if (state == HIGH) {
      docking = true;
    }
    else {
      docking = false;
    }
    //String dockingS = "Docking Status: "+String(docking)+" ";
    //Serial.println(dockingS);

    snprintf(msg, MSG_BUFFER_SIZE, "%d", docking);
    //Serial.print("Docking publish message: ");
    //Serial.println(msg);
    client.publish(mqtt_topic_docking, msg);
  }
}

void setup() {
  Serial.begin(9600);
	servo.attach(servoPin, 771, 2740);
	/*[Calibration] using min/max pulse widths of 771us and 2740us.
	  Different servos require different min/max settings.
    For an accurate 0 to 180 sweep */
  limitSwitch.setDebounceTime(50);
  servo.write(120);                 //set servo to initial position
  setup_wifi();
  client.setServer(mqtt_server, mqtt_port);
  client.setKeepAlive(65535);
}

void loop() {
  //Reconnect to MQTT broker if disconnected
  while (!client.connected()) {
    reconnect();
  }
  //Reconnect to WiFi if disconnected
  unsigned long currentMillis = millis();
  if ((WiFi.status() != WL_CONNECTED) && (currentMillis - previousMillis >=interval)) {
    //if WiFi is down, try reconnecting
    Serial.print(millis());
    Serial.println("Reconnecting to WiFi...");
    WiFi.disconnect();
    WiFi.reconnect();
    previousMillis = currentMillis;
  }

  //Check for status of robot's arrival
  while (!robot_arrived) {
    constantPublish();
    limitSwitch.loop();
    int state = limitSwitch.getState();
    if (state == HIGH) {
      //MQTT can only transmit strings
      docking = true;
      String dockingS = "Docking Status: "+String(docking)+" ";
      Serial.println(dockingS);
      //Serial.println(client.state()); //0 : MQTT_CONNECTED - the client is connected
      reconnect();
      delay(1000);
      //Publish to the MQTT Broker
      // unsigned long now = millis();
      // if (now - lastMsg > 10000) {
      //   lastMsg = now;
      if (client.publish(mqtt_topic_docking, String(dockingS).c_str())) {
        boolean rc = client.publish(mqtt_topic_docking, String(dockingS).c_str());
        Serial.println("Publishing Status: "+String(rc)+" ");
        Serial.println("Robot is receiving signal...");
        delay(2000);
      }
      else {
        Serial.println("Docking status failed to send. Reconnecting to MQTT Broker and trying again");
        reconnect();
        delay(10); // This delay ensures that client.publish doesn't clash with the client.connect call
        client.publish(mqtt_topic_docking, String(dockingS).c_str());
      }
      Serial.println("Limit switch activated! Robot is here, waiting for keypad input...");
      robot_arrived = true;
    }
    else {
      Serial.println("Robot has not arrived, waiting for robot...");
      delay(1000);      
    }
  }

  while (robot_arrived) {
    constantPublish();
    //Wait for valid input from keypad
    char key = keypad.getKey();
    while (key == NO_KEY || !(key >= '1' && key <= '6')) {
      constantPublish();
      key = keypad.getKey();
    }

    // Store keypad input if it's a valid table number
    if (key >= '1' && key <= '6') {
      tableNum = key - '0';
      //MQTT can only transmit strings
      String tableNumS = "Table No. for delivery: "+String(tableNum)+" ";
      Serial.println(tableNumS);
      //Serial.println(client.state()); //0 : MQTT_CONNECTED - the client is connected
      reconnect();
      delay(1000);
      //Publish to the MQTT Broker
      // unsigned long now = millis();
      // if (now - lastMsg > 10000) {
      //   lastMsg = now;
      if (client.publish(mqtt_topic_tablenum, String(tableNumS).c_str())) {
        boolean rc = client.publish(mqtt_topic_tablenum, String(tableNumS).c_str());
        Serial.println("Publishing Status: "+String(rc)+" ");
        Serial.println("Robot is receiving table number...");
        delay(1000);
        
        //Tilt bucket to transfer load can to robot
        Serial.println("Tilting...");
        delay(3000);
		    servo.write(20);
		    delay(3000);
        Serial.println("Returning to original position...");
		    servo.write(120);
        delay(2000);

        delay(1000);

        Serial.println("Can has been transferred. Robot is ready to deliver.");
        limitSwitch.loop();
        int state = limitSwitch.getState();
        while (state == HIGH) {
          constantPublish();
          Serial.println("Waiting for Robot to deliver...");
          delay(2000);
          limitSwitch.loop();
          state = limitSwitch.getState();
        }
        docking = false;
        String dockingS = "Docking Status: "+String(docking)+" ";
        Serial.println("Docking status: "+String(docking)+" ");
        //Serial.println(client.state()); //0 : MQTT_CONNECTED - the client is connected
        reconnect();
        delay(1000);
        //Publish to the MQTT Broker
        if (client.publish(mqtt_topic_docking, String(dockingS).c_str())) {
          boolean rc = client.publish(mqtt_topic_docking, String(dockingS).c_str());
          Serial.println("Publishing Status: "+String(rc)+" ");
          Serial.println("Docking status is sent!");
        }
        else {
          Serial.println("Docking status failed to send. Reconnecting to MQTT Broker and trying again");
          reconnect();
          delay(10); // This delay ensures that client.publish doesn't clash with the client.connect call
          client.publish(mqtt_topic_docking, String(dockingS).c_str());
        }
        Serial.println("Limit switch deactivated! Robot is delivering, waiting for next order.");
        robot_arrived = false;
      }
      //Again, client.publish will return a boolean value depending on whether it succeded or not.
      //If the message failed to send, we will try again, as the connection may have broken.
      else {
        Serial.println("Table No. failed to send. Reconnecting to MQTT Broker and trying again");
        reconnect();
        delay(10); // This delay ensures that client.publish doesn't clash with the client.connect call
        client.publish(mqtt_topic_tablenum, String(tableNumS).c_str());
      }        
    }
  }
}

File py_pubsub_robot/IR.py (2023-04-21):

import rclpy
import RPi.GPIO as GPIO
import time
GPIO.setmode(GPIO.BCM)
from rclpy.node import Node
from std_msgs.msg import String
Left_IR = 17 #GPIO 17 -> Left IR out
Right_IR = 9 #GPIO 9 -> Right IR out
#setup
GPIO.setup(Left_IR,GPIO.IN, pull_up_down=GPIO.PUD_DOWN)
GPIO.setup(Right_IR,GPIO.IN, pull_up_down=GPIO.PUD_DOWN)

class IRPublisher(Node):

    def __init__(self):
        super().__init__('IR_publisher')
        self.publisher_ = self.create_publisher(String, '/bot_IR', 10)
        timer_period = 0.5  # seconds
        self.timer = self.create_timer(timer_period, self.timer_callback)

    def timer_callback(self):
        msg = String()
        # 0=both not detected; 1=left detected; 2=right detected; 3=both detected
        if (not GPIO.input(Left_IR)) and (not GPIO.input(Right_IR)):
            msg.data = "0"
        elif GPIO.input(Left_IR) and (not GPIO.input(Right_IR)):
            msg.data = "1"
        elif (not GPIO.input(Left_IR)) and GPIO.input(Right_IR):
            msg.data = "2"
        elif GPIO.input(Left_IR) and GPIO.input(Right_IR):
            msg.data = "3"
        self.publisher_.publish(msg)
        self.get_logger().info('Publishing: "%s"' % msg.data)
        print(GPIO.input(Left_IR),GPIO.input(Right_IR))

def main(args=None):
    rclpy.init(args=args)
    IR_publisher = IRPublisher()
    rclpy.spin(IR_publisher)

    # Destroy the node explicitly
    # (optional - otherwise it will be done automatically
    # when the garbage collector destroys the node object)
    IR_publisher.destroy_node()
    rclpy.shutdown()


if __name__ == '__main__':
    main()

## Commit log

2023-03-21 Prints status of calibration, uncomented calibrationR in table1. Unresolved: calibrationR required 1 parameter but 2 given
2023-03-23 Removed 'self' parameter when calling calibrate
2023-03-30 modified calibration with smaller value of comparison added limit switch setup code
2023-04-01 Added calibration script, optimised navigations
2023-04-02 Moved limit switch to RPi
2023-04-02 Limit Switch script for bot & bot Limit Switch listener in table_nav
2023-04-03 calibrateR 0.2
    Changed turning movement to 1 degree pre turn.
    Edited "if" condition for turning (yet to test this version)
2023-04-03 Switch publisher v1
    Working code for publisher (on RPi, py_pubsub/limit_switch.py) and subscriber (in r2table_nav) for robot limit switch
2023-04-04 calibrateR 0.3
    calibrateR():
    Added abs() for alignment checking.
    Added 1.064 ratio for if conditions.
2023-04-04 Bot Limit Switch Subscriber v0.1
2023-04-05 bot_limit_status v0.1
    bot_limit_status():
    returns True when drink is filled in the robot (limit switch pressed) and vice versa.
2023-04-06 Added calibration for all directions
    Front: calibrateF()
    Back: calibrateB()
    Left: calibrateL()
    Right: calibrateR()
2023-04-07 Did some fine-tuning, added flexible calibration
2023-04-07 Added Odometry Calibration
2023-04-10 Included limit switch code
2023-04-11 Fixed MQTT bug,added limit switch & minor reroutes
2023-04-21 Created ESP32_Blink_onboard_LED
2023-04-21 Added ESP32 Test Scripts
2023-04-22 Added Electrical Circuit Diagrams
2023-04-22 Organized Electrical Circuits
2023-04-22 Updated ESP32 setup
2023-04-23 Deleted duplicates
    [Bucket Base_T5_QTY1.DXF]
2023-04-24 Removed duplicates
    [Side Support Bearing Side2_T5_QTY1.DXF]
